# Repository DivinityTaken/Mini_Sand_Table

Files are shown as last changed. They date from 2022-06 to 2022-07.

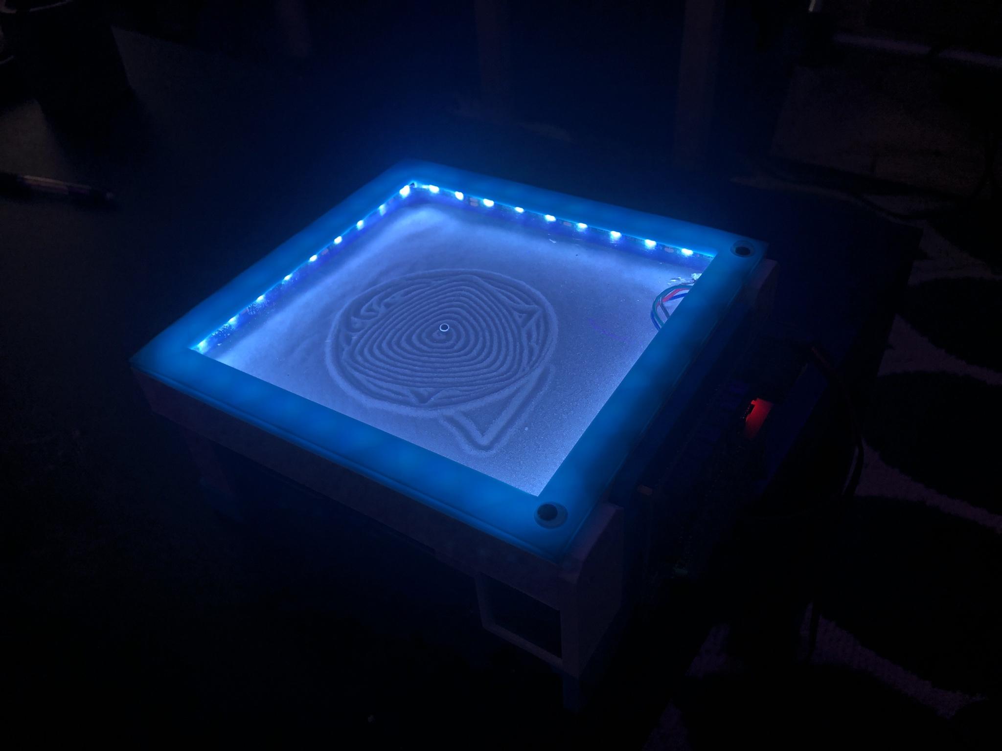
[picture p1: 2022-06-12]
Photos/Table Photo Lights.jpeg

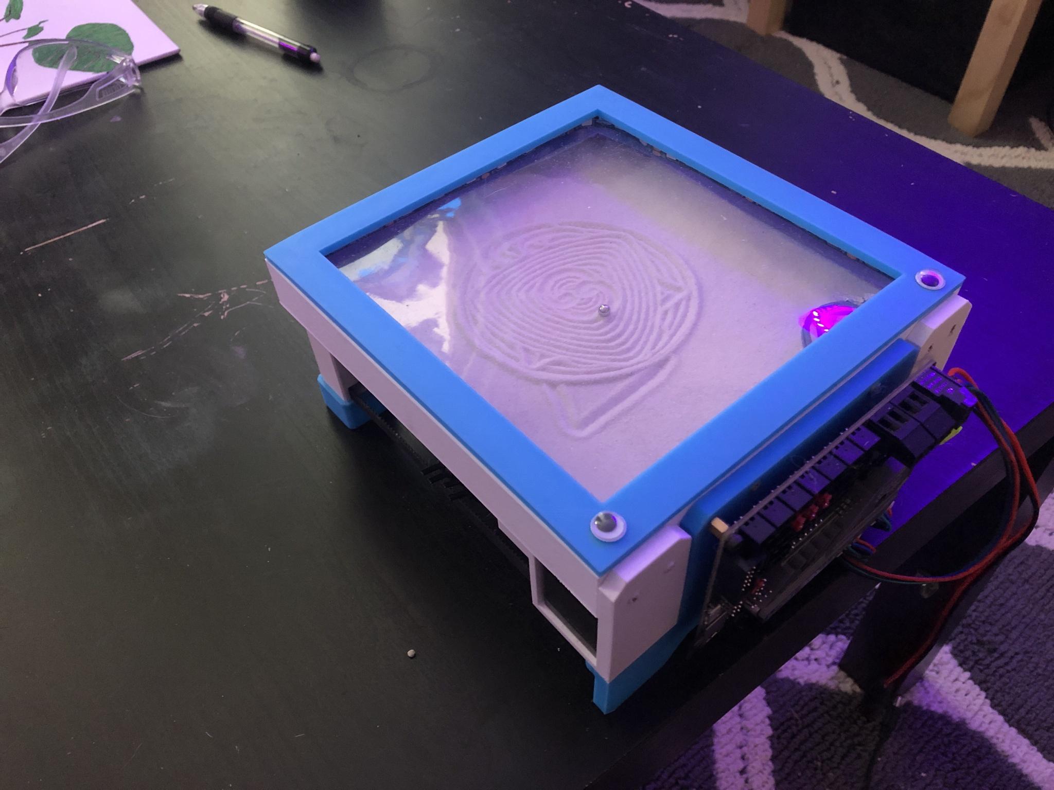
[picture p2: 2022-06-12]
Photos/Table Photo.jpeg

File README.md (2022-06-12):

# Mini_Sand_Table
This project started life as an assignment in one of my rapid prototyping classes however it has quickly grown into one of my favorite creations. The original idea was to build a scaled down Sisyphus Table that could sit on a desk as a little desk toy, this idea ended up being successful and the Mini Sand Table was born. 

BOM: [Link](https://docs.google.com/spreadsheets/d/1AzuKBqGoonScOun9C1d-WrM6_qlQOfSEnQ0_XetDFRE/edit?usp=sharing)

The links in the BOM are to AliExpress pages for the cheapest options, the doc will be updated later with Amazon links for easier and faster, but more expensive parts.

Printables: [Link](https://www.printables.com/model/224376-mini-sand-table)

The GitHub will always have the most up to date files, if I make any changes I will update the Printables page, but the GitHub syncs automatically so it'll end up being more up to date.

I used [Sandify](https://sandify.org/) to generate the GCODE for the table. It has a work area of 120x120mm so most of the patterns need to be scaled down. If you want the program to loop you'll have to add M808 L0 to the start GCODE and M808 to the end GCODE when you export from the website. If you are familiar with programming this is effectively a GOTO command, making the program go to the beginning when it gets to the end. More info can be found here: link.

The filename also has to be “auto0.g” for marlin to start running the program as soon as it boots up.

Some Notes:

* All of the parts (except for 1) are printable without supports 
* I recommend 100% infill for the “Sand Cover” piece to stop any light bleed
* The attached PDF is assembly instructions, if you have any feedback on the instructions please let me know

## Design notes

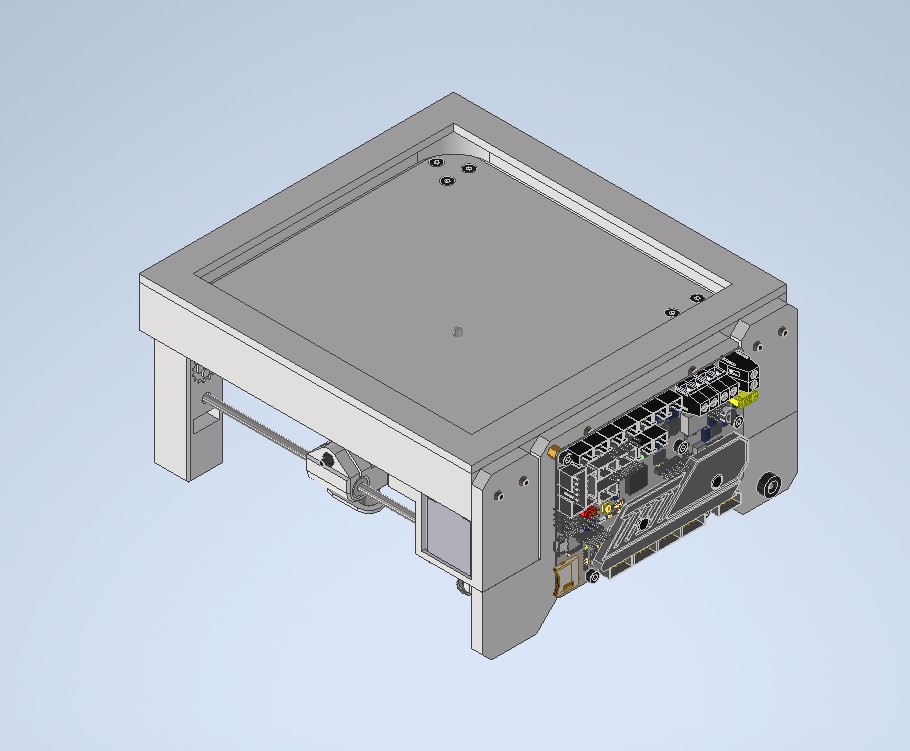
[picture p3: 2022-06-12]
Photos/Completed Model.jpg

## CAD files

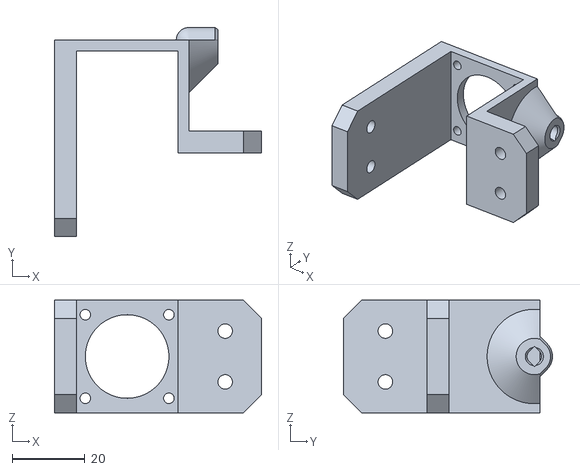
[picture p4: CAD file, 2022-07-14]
3D Printed/STL Files/Motor Mount.stl
57.0 x 57.5 x 31.0

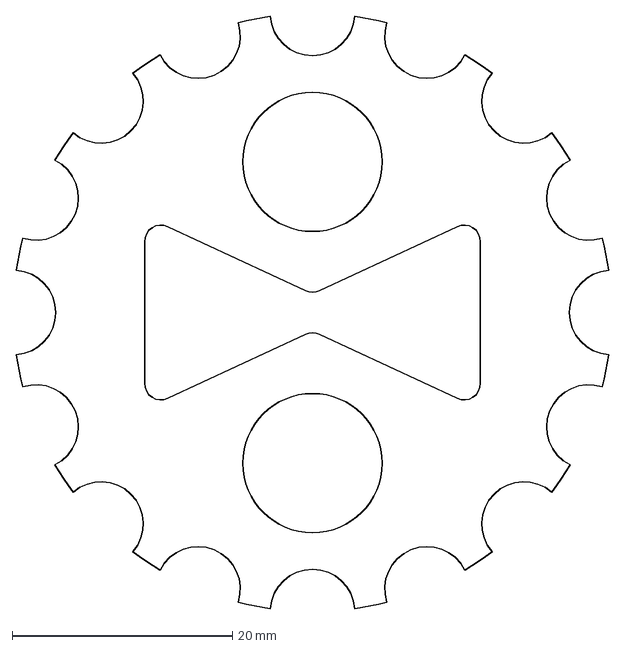
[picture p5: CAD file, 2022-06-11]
Logo.dxf
53.8 x 53.8 mm

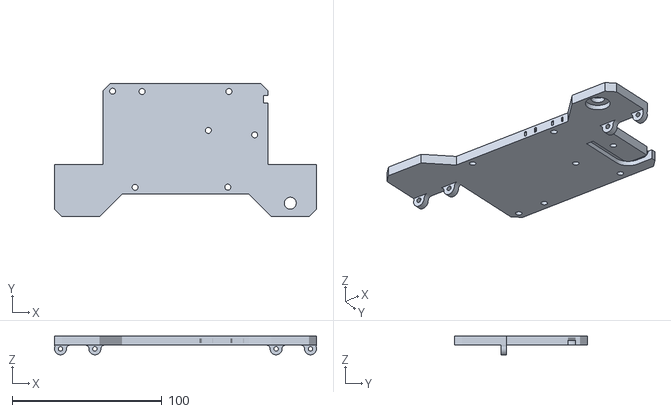
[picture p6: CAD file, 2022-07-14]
3D Printed/STL Files/Driver Board Mount.stl
175.0 x 89.0 x 12.5

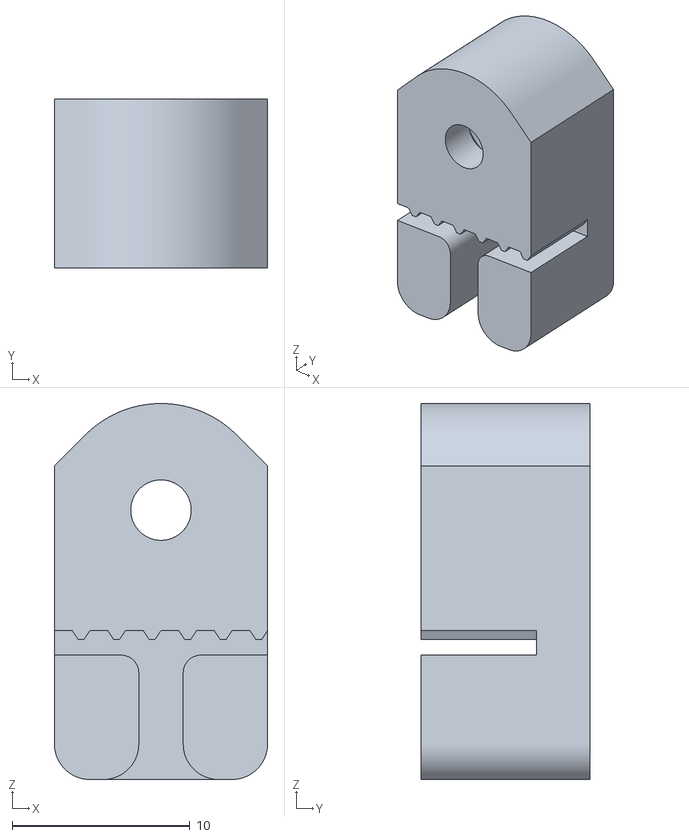
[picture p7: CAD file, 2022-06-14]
3D Printed/STL Files/Belt Clip.stl
12.0 x 9.50 x 21.2

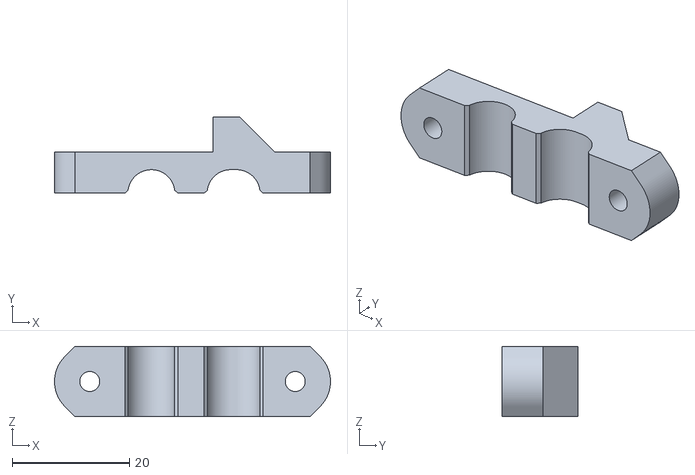
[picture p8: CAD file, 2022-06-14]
3D Printed/STL Files/Magnet Mount Lower.stl
47.0 x 13.0 x 12.0

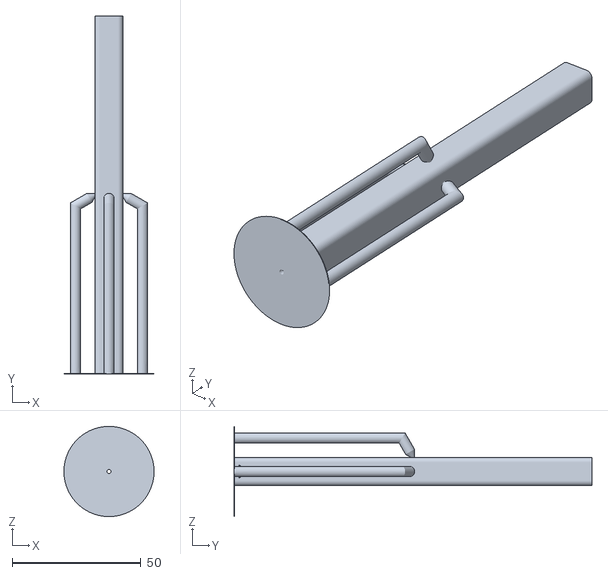
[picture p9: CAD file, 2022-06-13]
3D Printed/STL Files/140mm Rod Template.stl
35.0 x 139.0 x 35.0

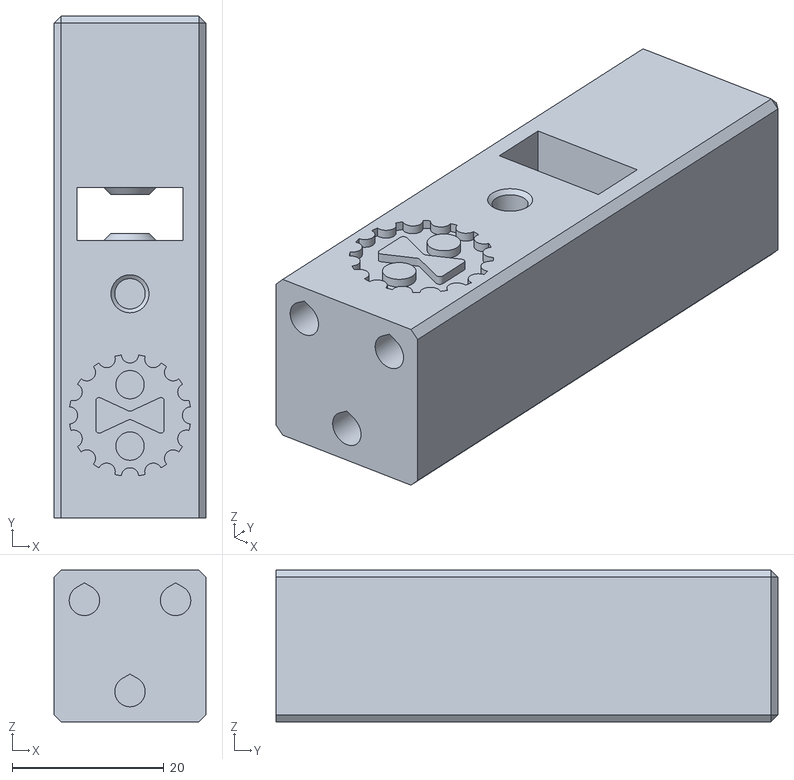
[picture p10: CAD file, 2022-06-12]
3D Printed/STL Files/Idle Bearing Mount.stl
20.0 x 66.1 x 20.0

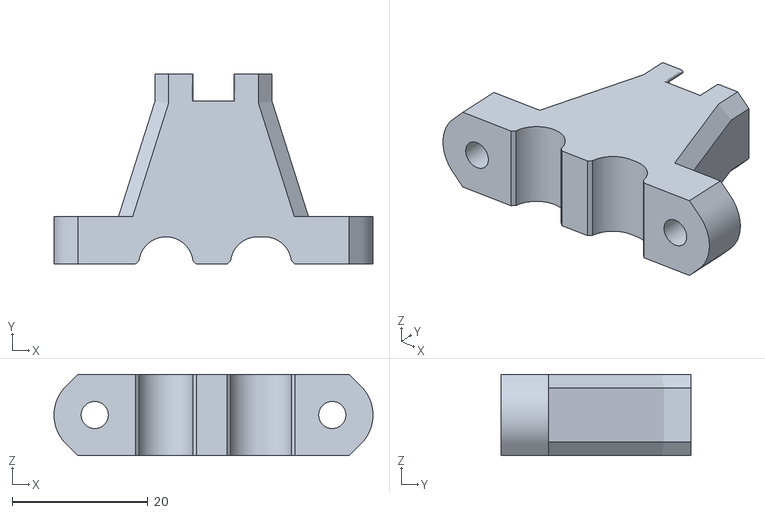
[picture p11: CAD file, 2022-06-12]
3D Printed/STL Files/Magnet Mount.stl
47.0 x 28.0 x 12.0

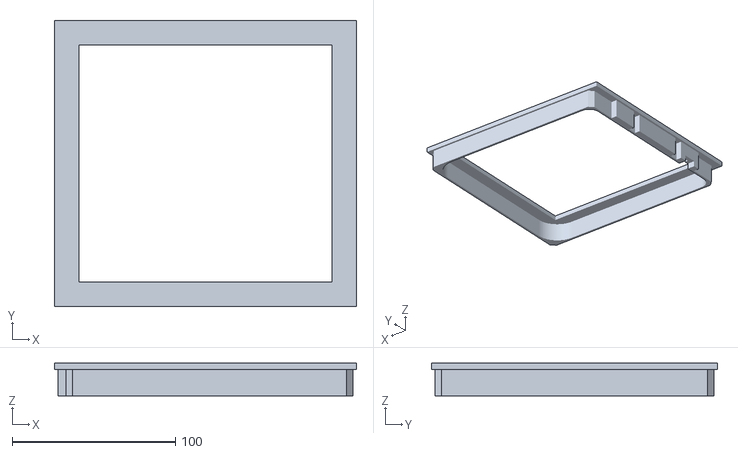
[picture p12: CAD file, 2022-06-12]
3D Printed/STL Files/Sand Cover.stl
185.0 x 175.0 x 20.0

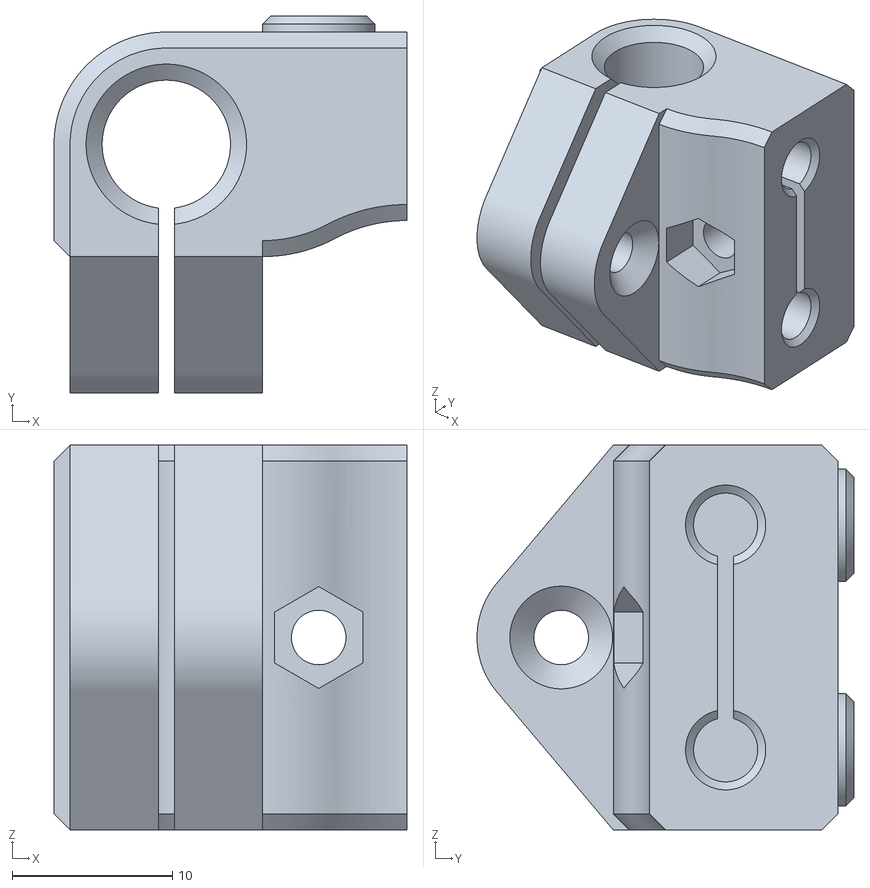
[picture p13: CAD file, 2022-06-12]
3D Printed/STL Files/XY Joiner.stl
22.0 x 23.5 x 24.0

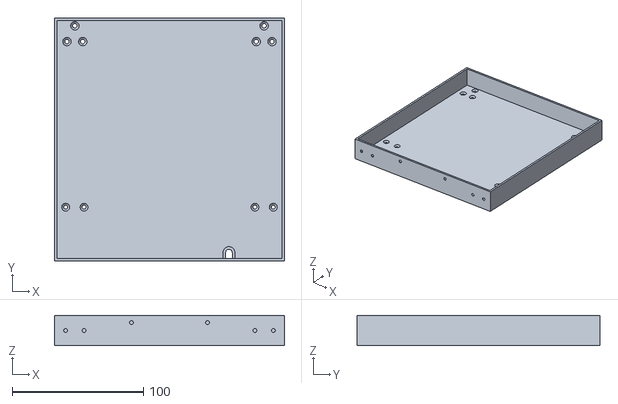
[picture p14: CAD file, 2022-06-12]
3D Printed/STL Files/Table Top.stl
175.0 x 185.0 x 23.0

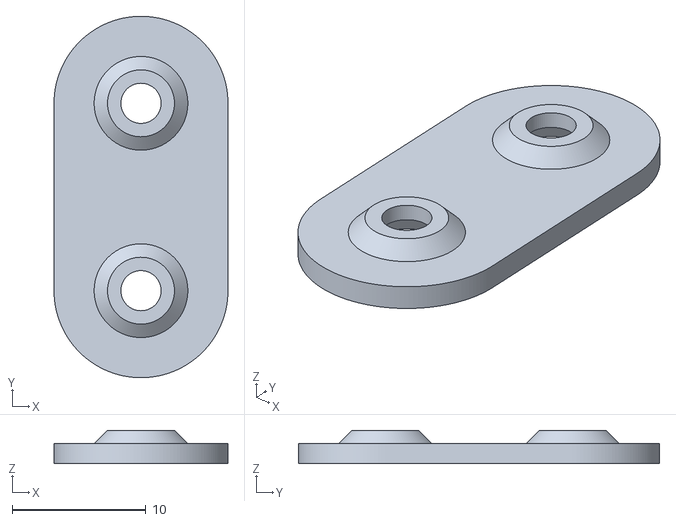
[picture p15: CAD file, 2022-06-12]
3D Printed/STL Files/Belt Retainer.stl
13.0 x 27.0 x 2.50

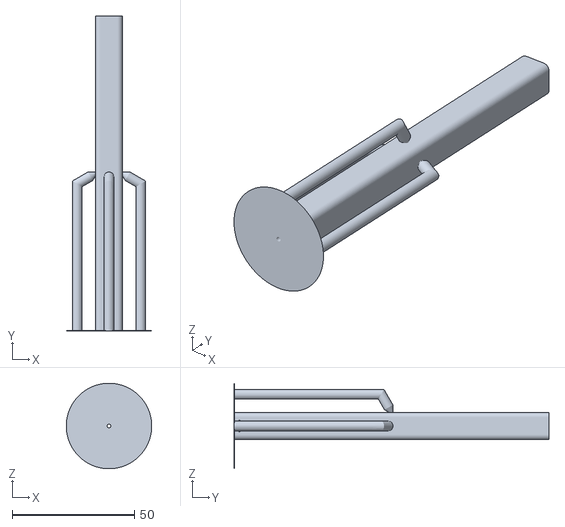
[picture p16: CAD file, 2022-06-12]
3D Printed/STL Files/130mm Rod Template.stl
35.0 x 129.0 x 35.0

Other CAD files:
3D Printed/130mm Rod Template.ipt
3D Printed/140mm Rod Template.ipt
3D Printed/Belt Clip.ipt
3D Printed/Belt Retainer.ipt
3D Printed/Driver Board Mount.ipt
3D Printed/Idle Bearing Mount.ipt
3D Printed/Magnet Mount Lower.ipt
3D Printed/Magnet Mount.ipt
3D Printed/Models with Heat Set Inserts/Driver Board Mount HSI.iam
3D Printed/Models with Heat Set Inserts/Idle Bearing Mount HSI.iam
3D Printed/Models with Heat Set Inserts/Magnet Mount HSI.iam
3D Printed/Models with Heat Set Inserts/Motor Mount HSI.iam
3D Printed/Models with Heat Set Inserts/OldVersions/Driver Board Mount HSI.0012.iam
3D Printed/Models with Heat Set Inserts/OldVersions/Idle Bearing Mount HSI.0009.iam
3D Printed/Models with Heat Set Inserts/OldVersions/Magnet Mount HSI.0007.iam
3D Printed/Models with Heat Set Inserts/OldVersions/Motor Mount HSI.0005.iam
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

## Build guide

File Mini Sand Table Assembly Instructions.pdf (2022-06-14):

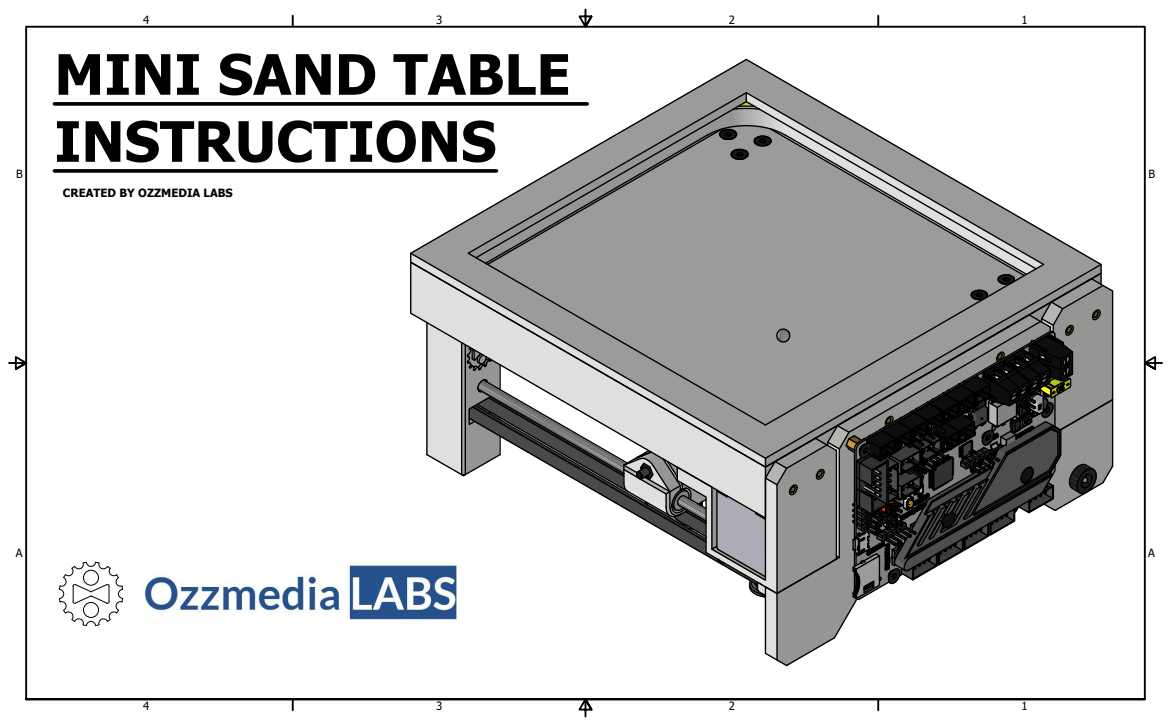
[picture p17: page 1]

MINI SAND TABLE
INSTRUCTIONS

CREATED BY OZZMEDIA LABS

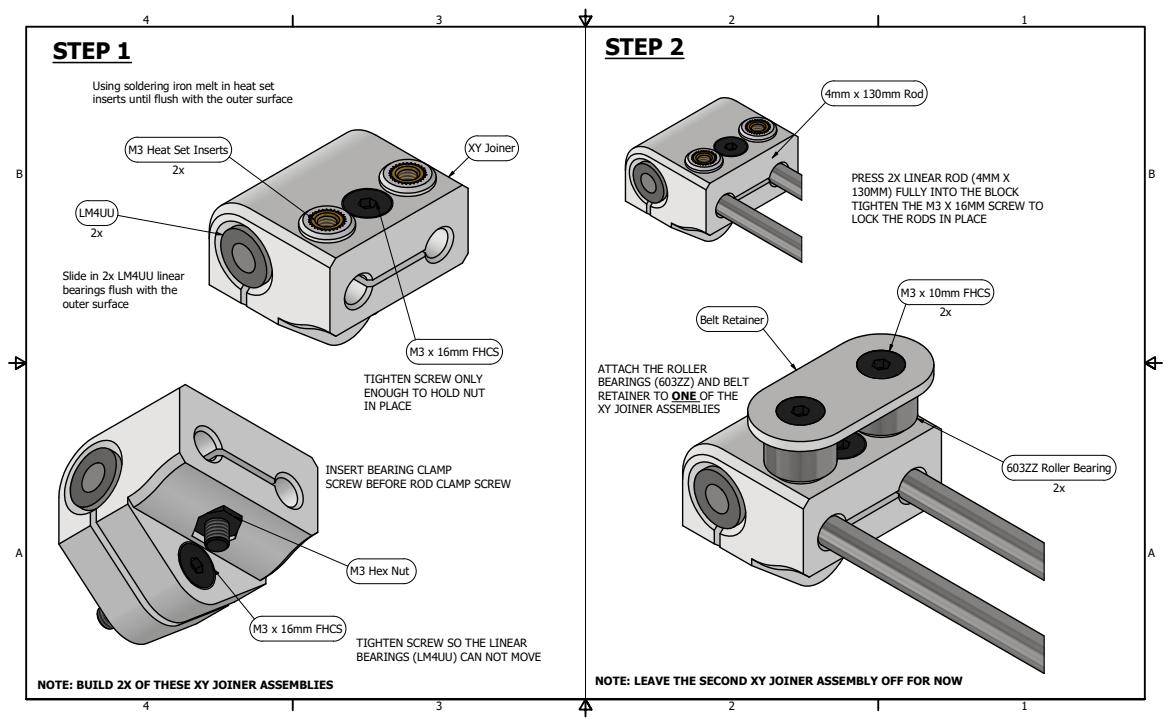
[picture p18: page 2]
XY Joiner; M3 x 16mm FHCS; M3 Hex Nut; 603ZZ Roller Bearing; M3 x 10mm FHCS; Belt Retainer; 4mm x 130mm Rod; STEP 1 STEP 2; NOTE: BUILD 2X OF THESE XY JOINER ASSEMBLIES; NOTE: LEAVE THE SECOND XY JOINER ASSEMBLY OFF FOR NOW

Using soldering iron melt in heat set
inserts until flush with the outer surface

M3 Heat Set Inserts

PRESS 2X LINEAR ROD (4MM X
130MM) FULLY INTO THE BLOCK
TIGHTEN THE M3 X 16MM SCREW TO
LOCK THE RODS IN PLACE

Slide in 2x LM4UU linear
bearings flush with the
outer surface

ATTACH THE ROLLER
BEARINGS (603ZZ) AND BELT
RETAINER TO ONE OF THE
XY JOINER ASSEMBLIES

TIGHTEN SCREW ONLY
ENOUGH TO HOLD NUT
IN PLACE

INSERT BEARING CLAMP
SCREW BEFORE ROD CLAMP SCREW

TIGHTEN SCREW SO THE LINEAR
BEARINGS (LM4UU) CAN NOT MOVE

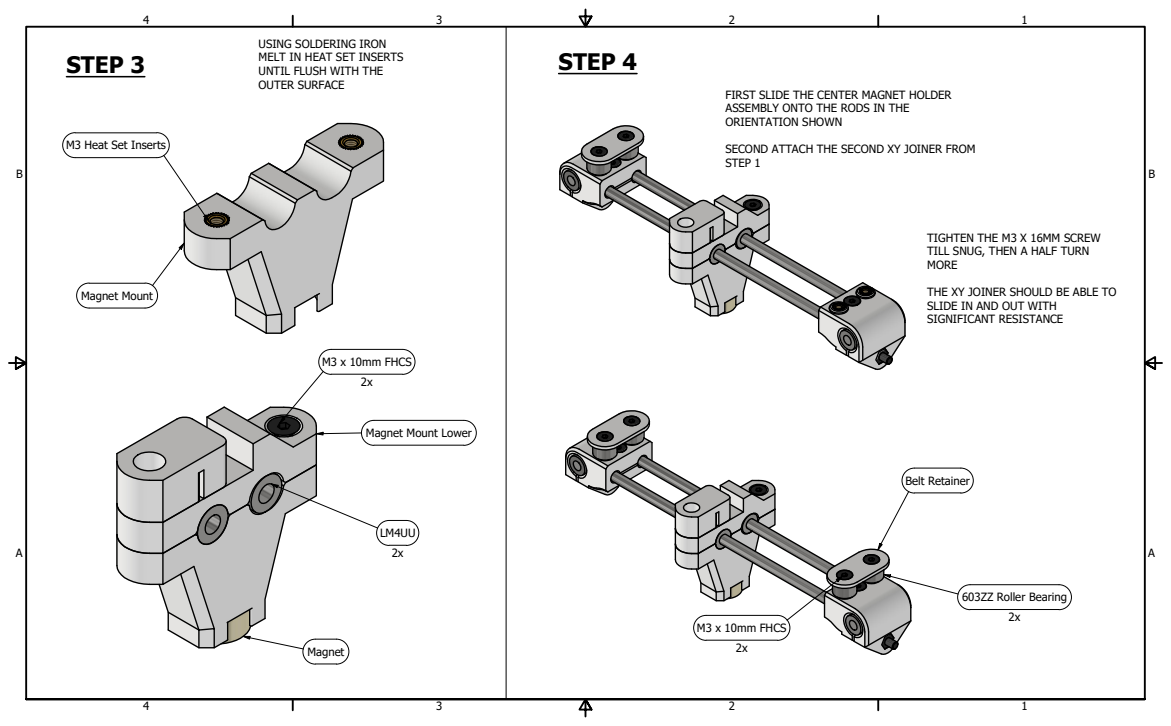
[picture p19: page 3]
Magnet Mount; M3 x 10mm FHCS; 603ZZ Roller Bearing; Belt Retainer; STEP 3 STEP 4

USING SOLDERING IRON
MELT IN HEAT SET INSERTS
UNTIL FLUSH WITH THE
OUTER SURFACE

FIRST SLIDE THE CENTER MAGNET HOLDER
ASSEMBLY ONTO THE RODS IN THE
ORIENTATION SHOWN

M3 Heat Set Inserts

SECOND ATTACH THE SECOND XY JOINER FROM
STEP 1

TIGHTEN THE M3 X 16MM SCREW
TILL SNUG, THEN A HALF TURN
MORE

THE XY JOINER SHOULD BE ABLE TO
SLIDE IN AND OUT WITH
SIGNIFICANT RESISTANCE

Magnet Mount Lower

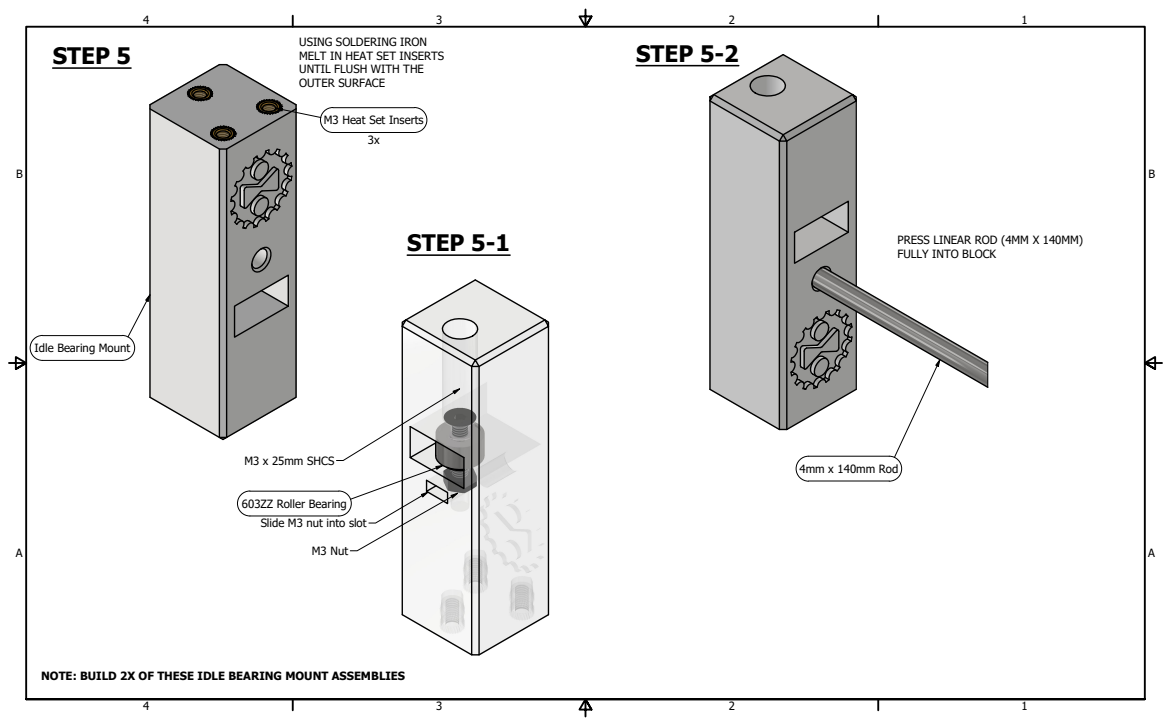
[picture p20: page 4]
M3 x 25mm SHCS; M3 Nut; 4mm x 140mm Rod; STEP 5; STEP 5-1; STEP 5-2

USING SOLDERING IRON
MELT IN HEAT SET INSERTS
UNTIL FLUSH WITH THE
OUTER SURFACE

M3 Heat Set Inserts

PRESS LINEAR ROD (4MM X 140MM)
FULLY INTO BLOCK

Idle Bearing Mount

603ZZ Roller Bearing
Slide M3 nut into slot

NOTE: BUILD 2X OF THESE IDLE BEARING MOUNT ASSEMBLIES

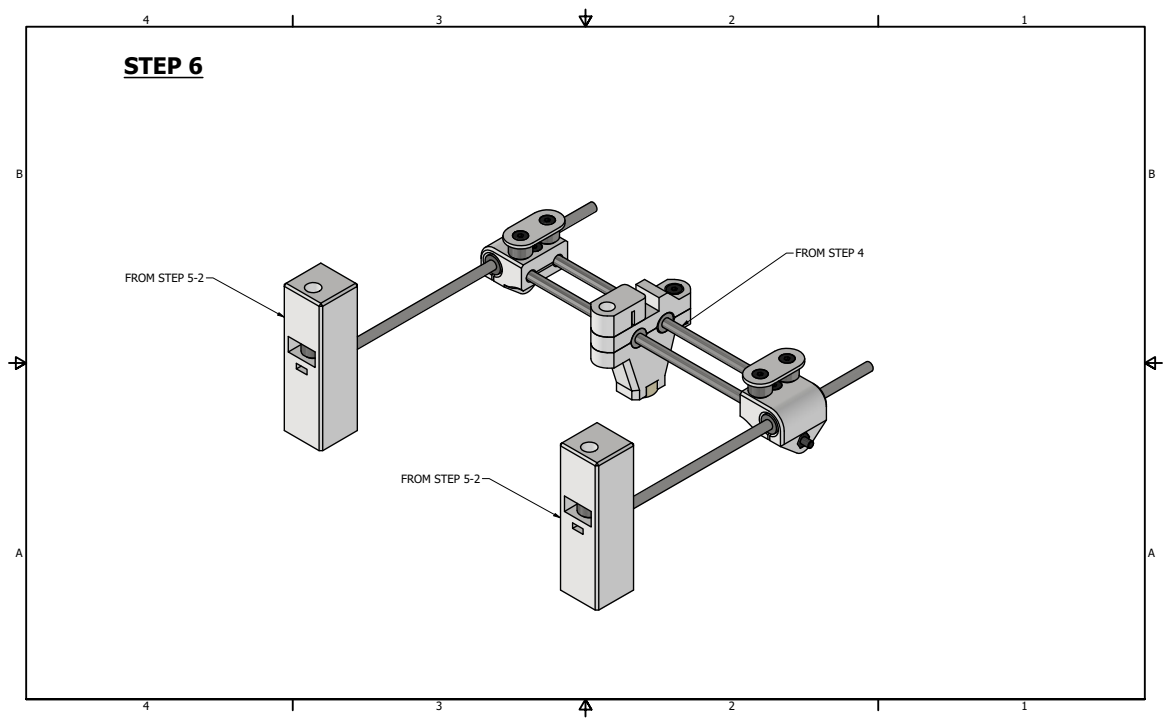
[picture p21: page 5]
FROM STEP 4; FROM STEP 5-2; STEP 6

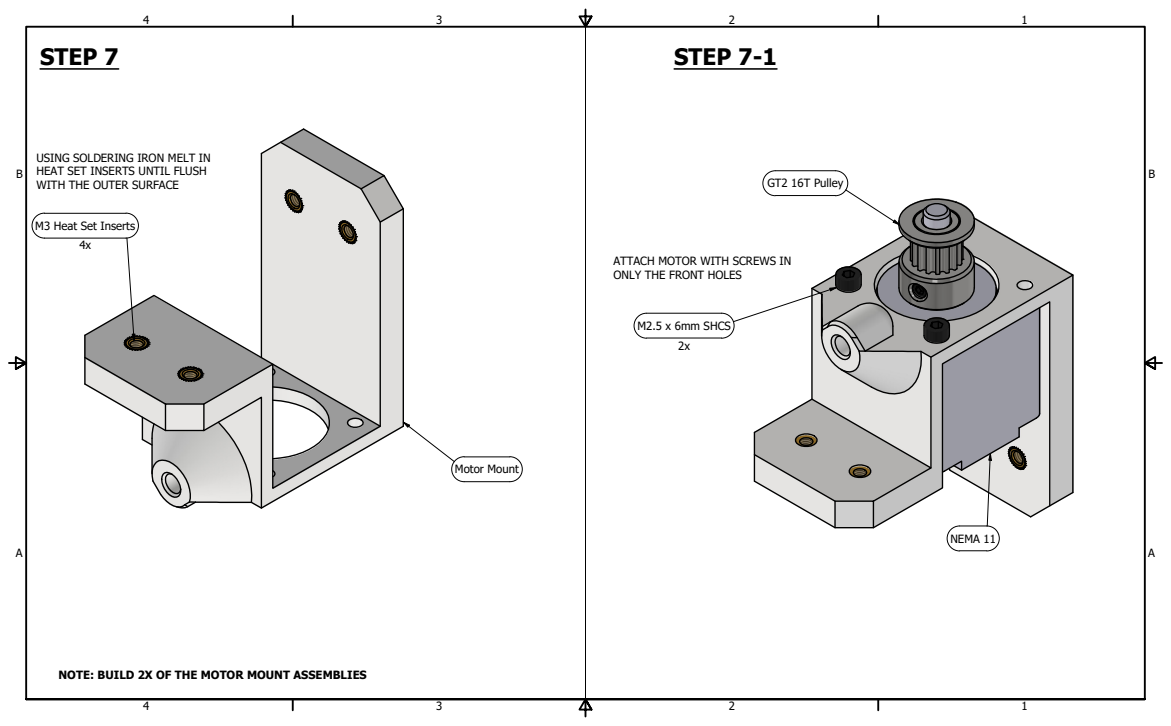
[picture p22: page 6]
Motor Mount; GT2 16T Pulley; M2.5 x 6mm SHCS; NEMA 11; STEP 7 STEP 7-1

USING SOLDERING IRON MELT IN
HEAT SET INSERTS UNTIL FLUSH
WITH THE OUTER SURFACE

M3 Heat Set Inserts

ATTACH MOTOR WITH SCREWS IN
ONLY THE FRONT HOLES

NOTE: BUILD 2X OF THE MOTOR MOUNT ASSEMBLIES

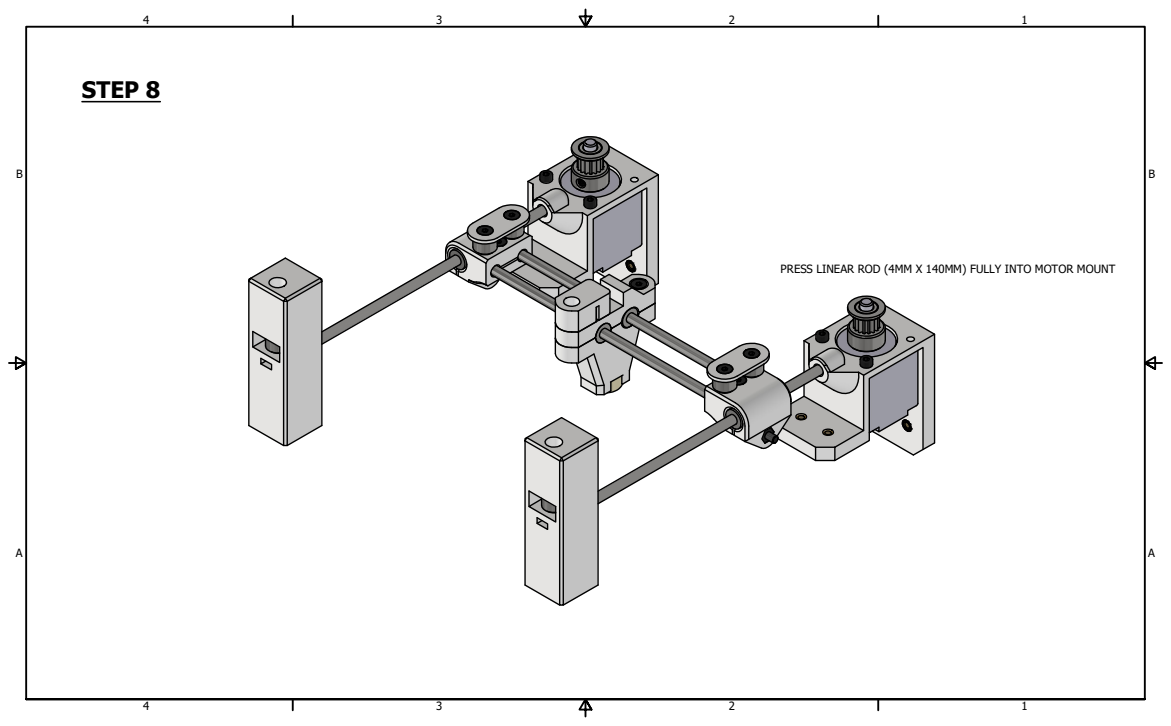
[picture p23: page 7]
STEP 8

PRESS LINEAR ROD (4MM X 140MM) FULLY INTO MOTOR MOUNT

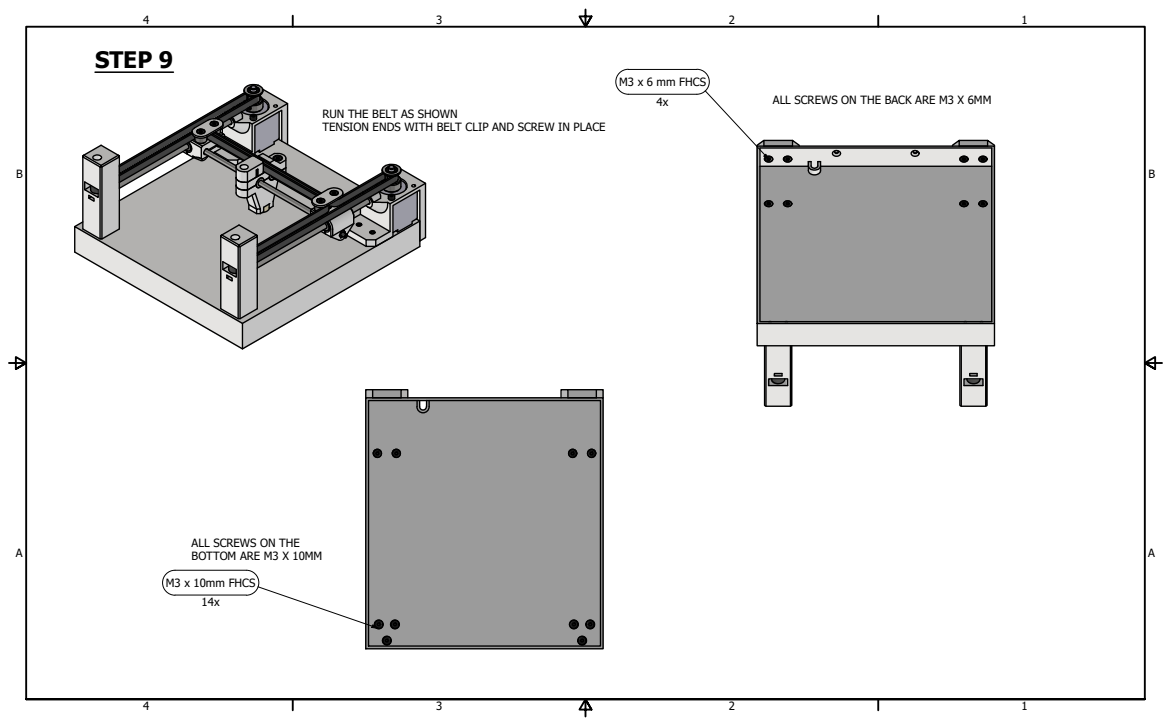
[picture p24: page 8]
M3 x 10mm FHCS; STEP 9; M3 x 6 mm FHCS; ALL SCREWS ON THE BACK ARE M3 X 6MM

RUN THE BELT AS SHOWN
TENSION ENDS WITH BELT CLIP AND SCREW IN PLACE

ALL SCREWS ON THE
BOTTOM ARE M3 X 10MM

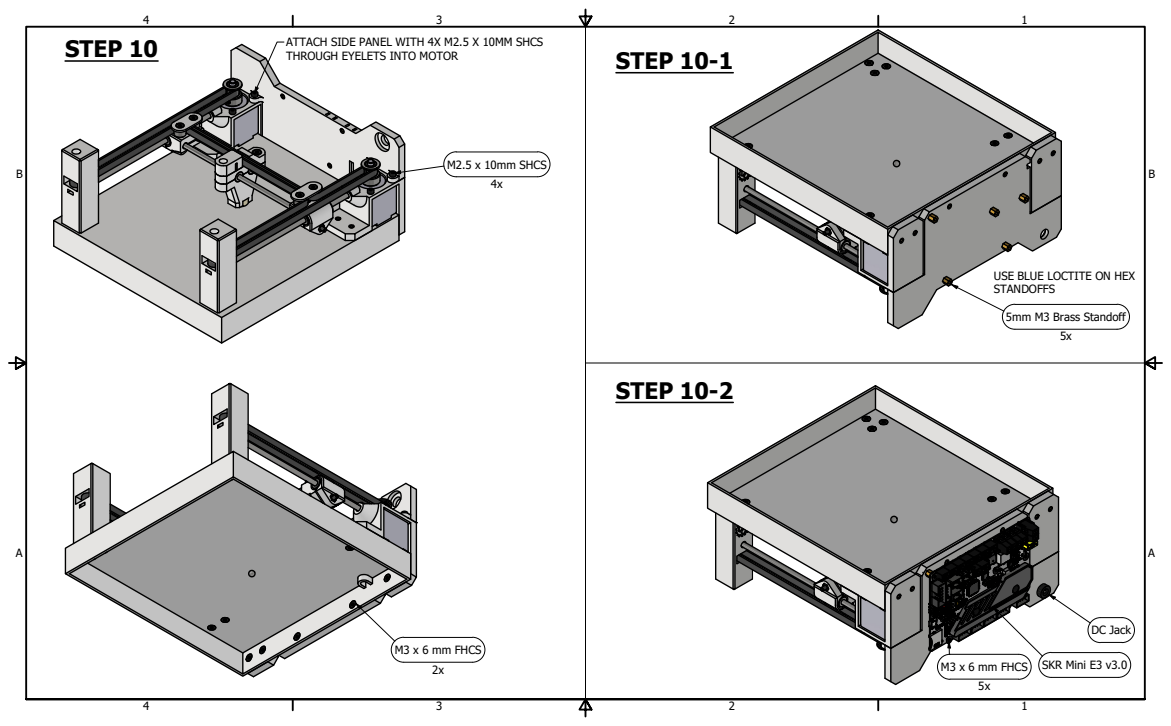
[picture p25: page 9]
M2.5 x 10mm SHCS; 5mm M3 Brass Standoff; SKR Mini E3 v3.0; STEP 10; STEP 10-1; STEP 10-2; DC Jack; M3 x 6 mm FHCS

ATTACH SIDE PANEL WITH 4X M2.5 X 10MM SHCS
THROUGH EYELETS INTO MOTOR

USE BLUE LOCTITE ON HEX
STANDOFFS

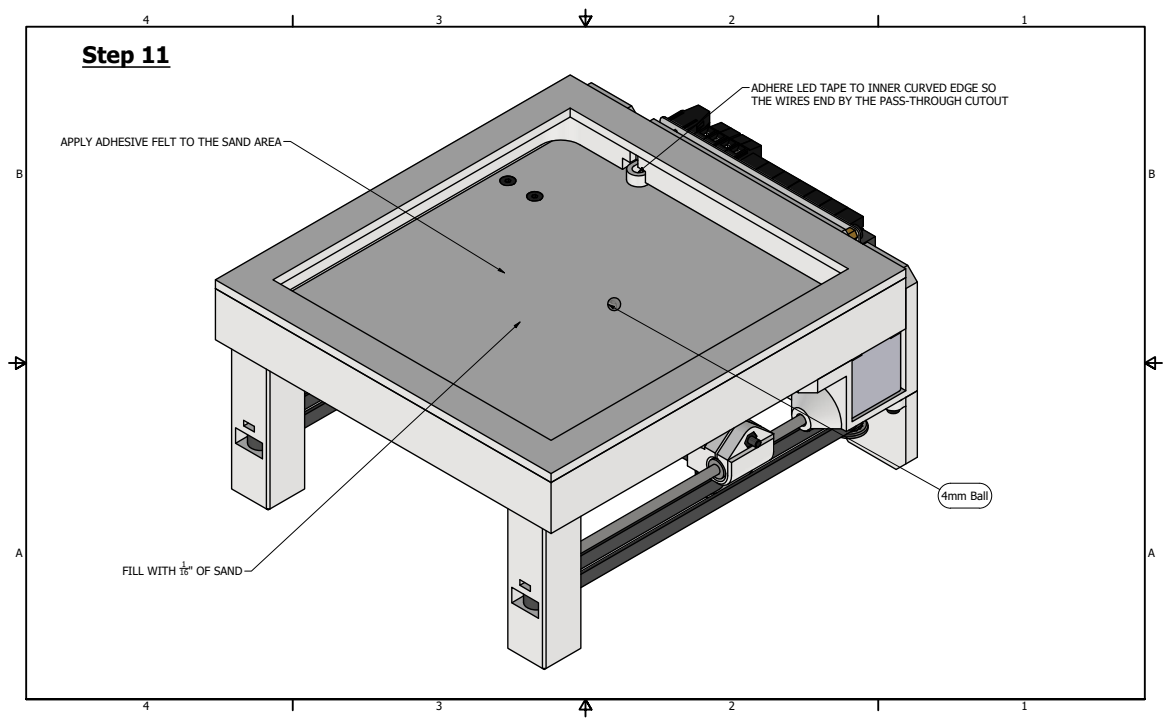
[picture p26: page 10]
Step 11; FILL WITH; 16" OF SAND; 4mm Ball

ADHERE LED TAPE TO INNER CURVED EDGE SO
THE WIRES END BY THE PASS-THROUGH CUTOUT

APPLY ADHESIVE FELT TO THE SAND AREA

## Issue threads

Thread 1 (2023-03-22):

Support part and guide missing.

cronos45, 2023-03-22:
What part needs support to print please and also are the rest of the guide somewhere I am not seeing?

DivinityTaken, 2023-03-23:
No supports are needed for any of the prints, the rest of the guide is a PDF in the root of the repo. The printables page also has the directions uploaded there.

cronos45, 2023-03-30:
Thank you @DivinityTaken

cronos45, 2023-04-01:
I can not find the marlin firmware used, I am unsure ho to set it up without endstops.

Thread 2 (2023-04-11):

homing

cronos45, 2023-04-11:
Hello, how do you get around the homing issue? Is there a change I need to make in the start Gcode? Also the marlin firm ware has the bed set to 200mm for X and Y should I leave that as it is?

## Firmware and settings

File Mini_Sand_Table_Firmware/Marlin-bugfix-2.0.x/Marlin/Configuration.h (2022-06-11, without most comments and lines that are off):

#pragma once
#define CONFIGURATION_H_VERSION 02010000
#define STRING_CONFIG_H_AUTHOR "(none, default config)" // Who made the changes.
#define SHOW_BOOTSCREEN
  #define MOTHERBOARD BOARD_BTT_SKR_MINI_E3_V3_0
#define SERIAL_PORT 1
#define BAUDRATE 250000
#define SERIAL_PORT_2 -1
#define BAUDRATE_2 250000   // Enable to override BAUDRATE
#define X_DRIVER_TYPE  TMC2209
#define Y_DRIVER_TYPE  TMC2209
#define Z_DRIVER_TYPE  TMC2209
#define E0_DRIVER_TYPE TMC2209
#define EXTRUDERS 1
#define DEFAULT_NOMINAL_FILAMENT_DIA 1.75
#define TEMP_SENSOR_0 1
#define TEMP_SENSOR_1 0
#define TEMP_SENSOR_2 0
#define TEMP_SENSOR_3 0
#define TEMP_SENSOR_4 0
#define TEMP_SENSOR_5 0
#define TEMP_SENSOR_6 0
#define TEMP_SENSOR_7 0
#define TEMP_SENSOR_BED 0
#define TEMP_SENSOR_PROBE 0
#define TEMP_SENSOR_CHAMBER 0
#define TEMP_SENSOR_COOLER 0
#define TEMP_SENSOR_BOARD 0
#define TEMP_SENSOR_REDUNDANT 0
#define DUMMY_THERMISTOR_998_VALUE  25
#define DUMMY_THERMISTOR_999_VALUE 100
#define TEMP_RESIDENCY_TIME         10  // (seconds) Time to wait for hotend to "settle" in M109
#define TEMP_WINDOW                  1  // (°C) Temperature proximity for the "temperature reached" timer
#define TEMP_HYSTERESIS              3  // (°C) Temperature proximity considered "close enough" to the target
#define TEMP_BED_RESIDENCY_TIME     10  // (seconds) Time to wait for bed to "settle" in M190
#define TEMP_BED_WINDOW              1  // (°C) Temperature proximity for the "temperature reached" timer
#define TEMP_BED_HYSTERESIS          3  // (°C) Temperature proximity considered "close enough" to the target
#define TEMP_CHAMBER_RESIDENCY_TIME 10  // (seconds) Time to wait for chamber to "settle" in M191
#define TEMP_CHAMBER_WINDOW          1  // (°C) Temperature proximity for the "temperature reached" timer
#define TEMP_CHAMBER_HYSTERESIS      3  // (°C) Temperature proximity considered "close enough" to the target
#if TEMP_SENSOR_REDUNDANT
  #define TEMP_SENSOR_REDUNDANT_SOURCE    E1  // The sensor that will provide the redundant reading.
  #define TEMP_SENSOR_REDUNDANT_TARGET    E0  // The sensor that we are providing a redundant reading for.
  #define TEMP_SENSOR_REDUNDANT_MAX_DIFF  10  // (°C) Temperature difference that will trigger a print abort.
#endif
#define HEATER_0_MINTEMP   5
#define HEATER_1_MINTEMP   5
#define HEATER_2_MINTEMP   5
#define HEATER_3_MINTEMP   5
#define HEATER_4_MINTEMP   5
#define HEATER_5_MINTEMP   5
#define HEATER_6_MINTEMP   5
#define HEATER_7_MINTEMP   5
#define BED_MINTEMP        5
#define CHAMBER_MINTEMP    5
#define HEATER_0_MAXTEMP 275
#define HEATER_1_MAXTEMP 275
#define HEATER_2_MAXTEMP 275
#define HEATER_3_MAXTEMP 275
#define HEATER_4_MAXTEMP 275
#define HEATER_5_MAXTEMP 275
#define HEATER_6_MAXTEMP 275
#define HEATER_7_MAXTEMP 275
#define BED_MAXTEMP      150
#define CHAMBER_MAXTEMP  60
#define HOTEND_OVERSHOOT 15   // (°C) Forbid temperatures over MAXTEMP - OVERSHOOT
#define BED_OVERSHOOT    10   // (°C) Forbid temperatures over MAXTEMP - OVERSHOOT
#define COOLER_OVERSHOOT  2   // (°C) Forbid temperatures closer than OVERSHOOT
#define PIDTEMP          // See the PID Tuning Guide at https://reprap.org/wiki/PID_Tuning
#define BANG_MAX 255     // Limits current to nozzle while in bang-bang mode; 255=full current
#define PID_MAX BANG_MAX // Limits current to nozzle while PID is active (see PID_FUNCTIONAL_RANGE below); 255=full current
#define PID_K1 0.95      // Smoothing factor within any PID loop
    #define DEFAULT_Kp  22.20
    #define DEFAULT_Ki   1.08
    #define DEFAULT_Kd 114.00
#define MAX_BED_POWER 255 // limits duty cycle to bed; 255=full current
#define MAX_CHAMBER_POWER 255 // limits duty cycle to chamber heater; 255=full current
  #define PID_FUNCTIONAL_RANGE 10 // If the temperature difference between the target temperature and the actual temperature
#define PREVENT_COLD_EXTRUSION
#define EXTRUDE_MINTEMP 170
#define PREVENT_LENGTHY_EXTRUDE
#define EXTRUDE_MAXLENGTH 200
#define THERMAL_PROTECTION_HOTENDS // Enable thermal protection for all extruders
#define THERMAL_PROTECTION_BED     // Enable thermal protection for the heated bed
#define THERMAL_PROTECTION_CHAMBER // Enable thermal protection for the heated chamber
#define THERMAL_PROTECTION_COOLER  // Enable thermal protection for the laser cooling
#define COREXY
#define USE_XMIN_PLUG
#define USE_YMIN_PLUG
#define USE_ZMIN_PLUG
#define ENDSTOPPULLUPS
#define X_MIN_ENDSTOP_INVERTING false // Set to true to invert the logic of the endstop.
#define Y_MIN_ENDSTOP_INVERTING false // Set to true to invert the logic of the endstop.
#define Z_MIN_ENDSTOP_INVERTING false // Set to true to invert the logic of the endstop.
#define I_MIN_ENDSTOP_INVERTING false // Set to true to invert the logic of the endstop.
#define J_MIN_ENDSTOP_INVERTING false // Set to true to invert the logic of the endstop.
#define K_MIN_ENDSTOP_INVERTING false // Set to true to invert the logic of the endstop.
#define U_MIN_ENDSTOP_INVERTING false // Set to true to invert the logic of the endstop.
#define V_MIN_ENDSTOP_INVERTING false // Set to true to invert the logic of the endstop.
#define W_MIN_ENDSTOP_INVERTING false // Set to true to invert the logic of the endstop.
#define X_MAX_ENDSTOP_INVERTING false // Set to true to invert the logic of the endstop.
#define Y_MAX_ENDSTOP_INVERTING false // Set to true to invert the logic of the endstop.
#define Z_MAX_ENDSTOP_INVERTING false // Set to true to invert the logic of the endstop.
#define I_MAX_ENDSTOP_INVERTING false // Set to true to invert the logic of the endstop.
#define J_MAX_ENDSTOP_INVERTING false // Set to true to invert the logic of the endstop.
#define K_MAX_ENDSTOP_INVERTING false // Set to true to invert the logic of the endstop.
#define U_MAX_ENDSTOP_INVERTING false // Set to true to invert the logic of the endstop.
#define V_MAX_ENDSTOP_INVERTING false // Set to true to invert the logic of the endstop.
#define W_MAX_ENDSTOP_INVERTING false // Set to true to invert the logic of the endstop.
#define Z_MIN_PROBE_ENDSTOP_INVERTING false // Set to true to invert the logic of the probe.
#define DEFAULT_AXIS_STEPS_PER_UNIT   { 80, 80, 400, 500 }
#define DEFAULT_MAX_FEEDRATE          { 300, 300, 5, 25 }
#define DEFAULT_MAX_ACCELERATION      { 3000, 3000, 100, 10000 }
#define DEFAULT_ACCELERATION          3000    // X, Y, Z and E acceleration for printing moves
#define DEFAULT_RETRACT_ACCELERATION  3000    // E acceleration for retracts
#define DEFAULT_TRAVEL_ACCELERATION   3000    // X, Y, Z acceleration for travel (non printing) moves
#define DEFAULT_EJERK    5.0  // May be used by Linear Advance
  #define JUNCTION_DEVIATION_MM 0.013 // (mm) Distance from real junction edge
  #define JD_HANDLE_SMALL_SEGMENTS    // Use curvature estimation instead of just the junction angle
#define Z_MIN_PROBE_USES_Z_MIN_ENDSTOP_PIN
#define NOZZLE_TO_PROBE_OFFSET { 10, 10, 0 }
#define PROBING_MARGIN 10
#define XY_PROBE_FEEDRATE (133*60)
#define Z_PROBE_FEEDRATE_FAST (4*60)
#define Z_PROBE_FEEDRATE_SLOW (Z_PROBE_FEEDRATE_FAST / 2)
#define Z_CLEARANCE_DEPLOY_PROBE   10 // Z Clearance for Deploy/Stow
#define Z_CLEARANCE_BETWEEN_PROBES  5 // Z Clearance between probe points
#define Z_CLEARANCE_MULTI_PROBE     5 // Z Clearance between multiple probes
#define Z_PROBE_LOW_POINT          -2 // Farthest distance below the trigger-point to go before stopping
#define Z_PROBE_OFFSET_RANGE_MIN -20
#define Z_PROBE_OFFSET_RANGE_MAX 20
#define X_ENABLE_ON 0
#define Y_ENABLE_ON 0
#define Z_ENABLE_ON 0
#define E_ENABLE_ON 0 // For all extruders
#define DISABLE_X false
#define DISABLE_Y false
#define DISABLE_Z false
#define DISABLE_E false             // Disable the extruder when not stepping
#define DISABLE_INACTIVE_EXTRUDER   // Keep only the active extruder enabled
#define INVERT_X_DIR false
#define INVERT_Y_DIR true
#define INVERT_Z_DIR false
#define INVERT_E0_DIR false
#define INVERT_E1_DIR false
#define INVERT_E2_DIR false
#define INVERT_E3_DIR false
#define INVERT_E4_DIR false
#define INVERT_E5_DIR false
#define INVERT_E6_DIR false
#define INVERT_E7_DIR false
#define X_HOME_DIR -1
#define Y_HOME_DIR -1
#define Z_HOME_DIR -1
#define X_BED_SIZE 200
#define Y_BED_SIZE 200
#define X_MIN_POS 0
#define Y_MIN_POS 0
#define Z_MIN_POS 0
#define X_MAX_POS X_BED_SIZE
#define Y_MAX_POS Y_BED_SIZE
#define Z_MAX_POS 200
#define MIN_SOFTWARE_ENDSTOPS
  #define MIN_SOFTWARE_ENDSTOP_X
  #define MIN_SOFTWARE_ENDSTOP_Y
  #define MIN_SOFTWARE_ENDSTOP_Z
  #define MIN_SOFTWARE_ENDSTOP_I
  #define MIN_SOFTWARE_ENDSTOP_J
  #define MIN_SOFTWARE_ENDSTOP_K
  #define MIN_SOFTWARE_ENDSTOP_U
  #define MIN_SOFTWARE_ENDSTOP_V
  #define MIN_SOFTWARE_ENDSTOP_W
#define MAX_SOFTWARE_ENDSTOPS
  #define MAX_SOFTWARE_ENDSTOP_X
  #define MAX_SOFTWARE_ENDSTOP_Y
  #define MAX_SOFTWARE_ENDSTOP_Z
  #define MAX_SOFTWARE_ENDSTOP_I
  #define MAX_SOFTWARE_ENDSTOP_J
  #define MAX_SOFTWARE_ENDSTOP_K
  #define MAX_SOFTWARE_ENDSTOP_U
  #define MAX_SOFTWARE_ENDSTOP_V
  #define MAX_SOFTWARE_ENDSTOP_W
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

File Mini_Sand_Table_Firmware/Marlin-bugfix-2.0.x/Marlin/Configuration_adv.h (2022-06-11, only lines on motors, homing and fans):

#define E0_AUTO_FAN_PIN -1
#define E1_AUTO_FAN_PIN -1
#define E2_AUTO_FAN_PIN -1
#define E3_AUTO_FAN_PIN -1
#define E4_AUTO_FAN_PIN -1
#define E5_AUTO_FAN_PIN -1
#define E6_AUTO_FAN_PIN -1
#define E7_AUTO_FAN_PIN -1
#define CHAMBER_AUTO_FAN_PIN -1
#define COOLER_AUTO_FAN_PIN -1
#define HOMING_BUMP_MM      { 5, 5, 2 }       // (linear=mm, rotational=°) Backoff from endstops after first bump
#define HOMING_BUMP_DIVISOR { 2, 2, 4 }       // Re-Bump Speed Divisor (Divides the Homing Feedrate)
#define MICROSTEP_MODES { 16, 16, 16, 16, 16, 16 } // [1,2,4,8,16]
    #define X_CURRENT       200        // (mA) RMS current. Multiply by 1.414 for peak current.
    #define X_CURRENT_HOME  X_CURRENT  // (mA) RMS current for sensorless homing
    #define X_MICROSTEPS     16        // 0..256
    #define Y_CURRENT       200
    #define Y_CURRENT_HOME  Y_CURRENT
    #define Y_MICROSTEPS     16
    #define Z_CURRENT       800
    #define Z_CURRENT_HOME  Z_CURRENT
    #define Z_MICROSTEPS     16
    #define E0_CURRENT      800
    #define E0_MICROSTEPS    16
  #define X_HYBRID_THRESHOLD     100  // [mm/s]
  #define X2_HYBRID_THRESHOLD    100
  #define Y_HYBRID_THRESHOLD     100
  #define Y2_HYBRID_THRESHOLD    100
  #define Z_HYBRID_THRESHOLD       3
  #define Z2_HYBRID_THRESHOLD      3
  #define Z3_HYBRID_THRESHOLD      3
  #define Z4_HYBRID_THRESHOLD      3
  #define I_HYBRID_THRESHOLD       3  // [linear=mm/s, rotational=°/s]
  #define J_HYBRID_THRESHOLD       3  // [linear=mm/s, rotational=°/s]
  #define K_HYBRID_THRESHOLD       3  // [linear=mm/s, rotational=°/s]
  #define U_HYBRID_THRESHOLD       3  // [mm/s]
  #define V_HYBRID_THRESHOLD       3
  #define W_HYBRID_THRESHOLD       3
  #define E0_HYBRID_THRESHOLD     30
  #define E1_HYBRID_THRESHOLD     30
  #define E2_HYBRID_THRESHOLD     30
  #define E3_HYBRID_THRESHOLD     30
  #define E4_HYBRID_THRESHOLD     30
  #define E5_HYBRID_THRESHOLD     30
  #define E6_HYBRID_THRESHOLD     30
  #define E7_HYBRID_THRESHOLD     30
  #define SENSORLESS_HOMING // StallGuard capable drivers only
    #define X_STALL_SENSITIVITY  8
    #define X2_STALL_SENSITIVITY X_STALL_SENSITIVITY
    #define Y_STALL_SENSITIVITY  8
    #define Y2_STALL_SENSITIVITY Y_STALL_SENSITIVITY

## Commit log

2022-04-23 Initial Upload
    [4mm x 130mm Rod.0004.ipt, 4mm x 130mm Rod.ipt, 4mm x 140mm Rod.0002.ipt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]
2022-04-29 Modified Attachment method
    [Ball.0001.ipt, Ball.ipt, Magnet.ipt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]
2022-06-12 Add STL
    [130mm Rod Template.stl, Belt Retainer.stl, Driver Board Mount.stl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]
2022-06-12 Added Belt and LED Tape
    [GT2 Belt.0006.ipt, GT2 Belt.ipt, Led Tape.0003.ipt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]
2022-06-13 Add template
    [140mm Rod Template.0006.ipt, 140mm Rod Template.ipt, 140mm Rod Template.stl]
2022-06-14 redid belt tensioner
    [Belt Clip.0012.ipt, Belt Clip.ipt, GT2 Belt.0012.ipt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]
2022-06-14 export new STL
    [Belt Clip.stl, Magnet Mount Lower.stl]

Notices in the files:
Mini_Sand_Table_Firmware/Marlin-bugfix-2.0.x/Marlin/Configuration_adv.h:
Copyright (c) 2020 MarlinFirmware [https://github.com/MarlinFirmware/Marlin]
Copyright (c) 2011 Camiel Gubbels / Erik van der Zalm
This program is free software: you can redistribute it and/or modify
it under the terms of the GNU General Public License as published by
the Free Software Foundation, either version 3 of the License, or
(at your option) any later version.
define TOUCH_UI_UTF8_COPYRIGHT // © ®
